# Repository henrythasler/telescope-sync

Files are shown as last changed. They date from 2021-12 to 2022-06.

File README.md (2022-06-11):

# Upgrading a Dobsonian-Telescope with Push-To Capabilities

This is about retrofitting a [Dobsonian Telescope](https://en.wikipedia.org/wiki/Dobsonian_telescope) with fancy electronics and means to indicate where the telescope is pointing at, to allow the observer to quickly find an object in the night sky. My motivation was born on a very cold evening shortly after I bought the telescope and I desparately tried to find Uranus in the night sky - and failed.

The resulting setup can, for example, be used with the excellent [Stellarium Plus](https://www.stellarium-labs.com/stellarium-mobile-plus/) App. 

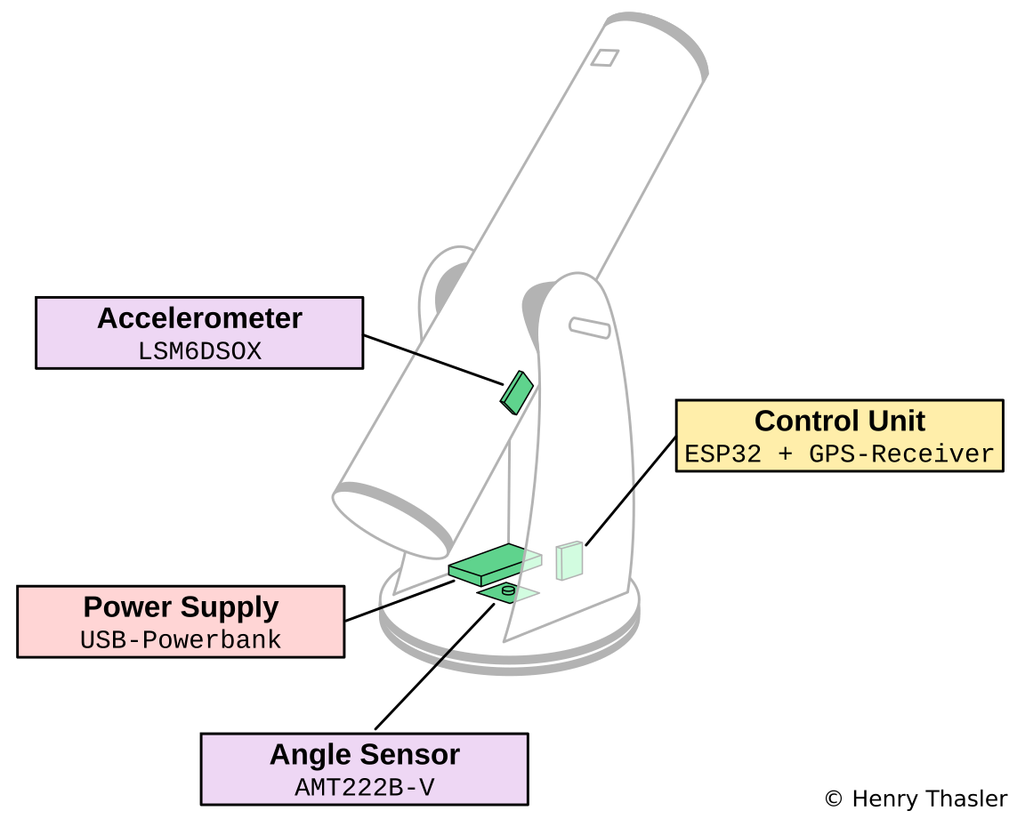
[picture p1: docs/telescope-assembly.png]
Telescope Assembly


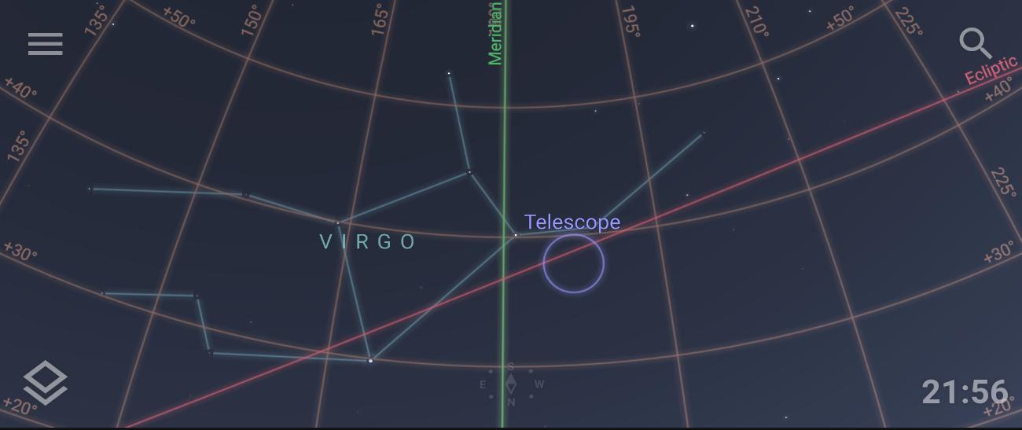
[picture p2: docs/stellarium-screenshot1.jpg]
Stellarium Screenshot


## Quick-Start-Guide

1. Connect power supply.
2. Connect Stellarium Plus via Bluetooth.
3. Wait for GPS location fix.
4. Point the telescope to a known target and set alignment point via Stellarium App.
5. Repeat step 4 to increase alignment precision.

## Introduction

A [Dobsonian Telescope](https://en.wikipedia.org/wiki/Dobsonian_telescope) is a type of telescope that uses an alt-azimuth mounting, which means you can rotate and tilt it. I'm using a [Sky-Watcher 8" Traditional](http://skywatcher.com/product/dob-8-traditional/) but the general method described here can be applied to any Dobsonian.

The term Push-to is generally referred to as a method to indicate (e.g. on a Smartphone-App) where the telescope is pointing at and thus allows to quickly find an object. 

The main design goals are:

1. Precision - I want this setup to be as precise a I can make it with hardware that is available to a hobbyist. 
2. Integration - The solution should integrate with existing astronomy-apps or -software.
3. Simplicity - Setup and installation must match the mobility of a Dobsonian telescope.
4. Wireless - No wires are needed to connect the user interface. Use Wifi or Bluetooth.
5. Ease-of-Use - Anyone should be able to use it with minimal guidance.

## General Concept

To map the current orientation of the telescope to a map of the night sky, we need the following information:

- Date and time
- Location
- Orientation of the telescope

With this information we can transform the orientation of the telescope from a horizontal (alt-azimuth) coordinate system to the equatorial coordinate system that astronomy apps use to indicate the actual position in the night sky where the telescope is pointing at. The critical information with the most influence on the resulting overall precision is the telescope's orientation.

## Overall Design and Result

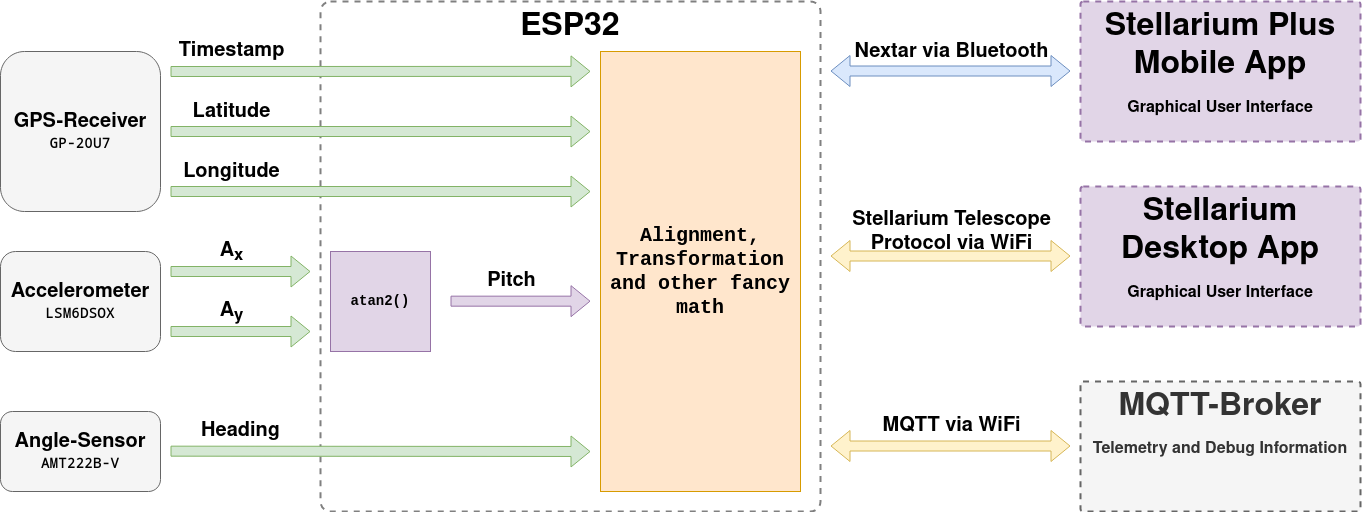
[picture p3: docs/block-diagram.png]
Block Diagram


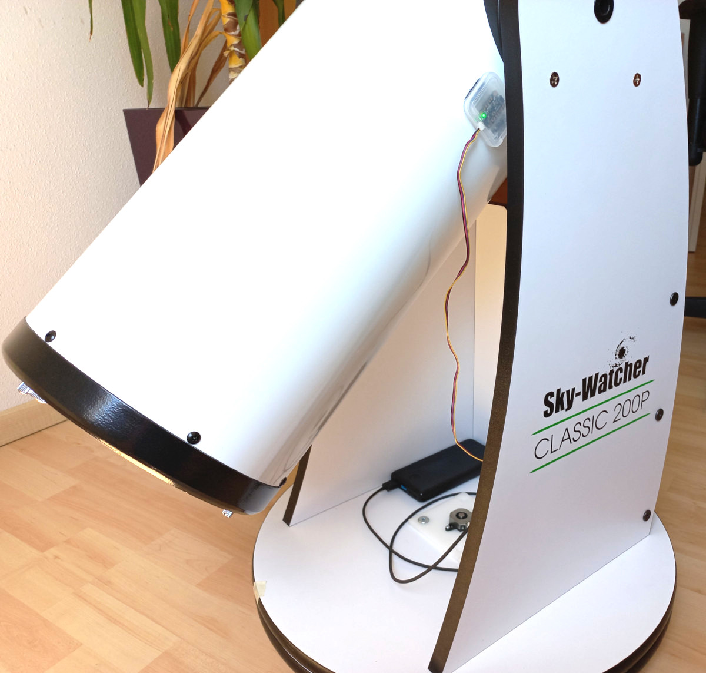
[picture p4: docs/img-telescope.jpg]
Telescope Picture
 

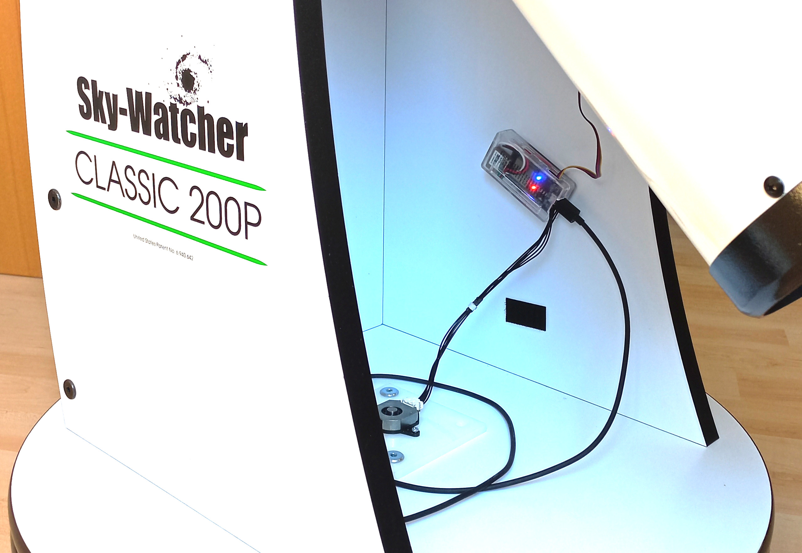
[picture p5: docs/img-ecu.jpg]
ECU Picture


### Stationary precision, noise

Pitch is filtered with 50-samples moving-average:

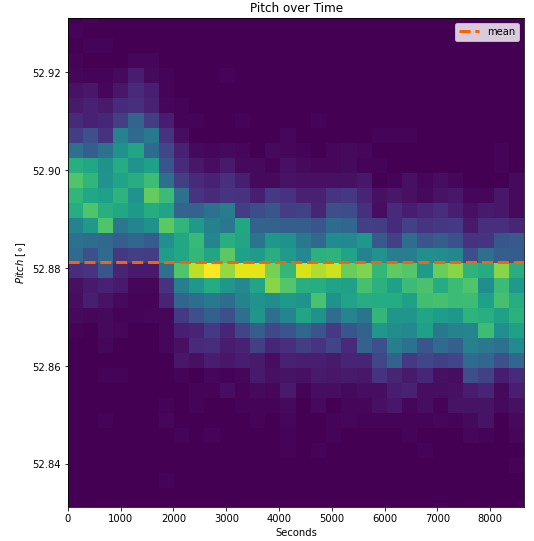
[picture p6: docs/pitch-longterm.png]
Chart Pitch Longterm


Heading is filtered with a simple IIR-Filter (decay=0.7):

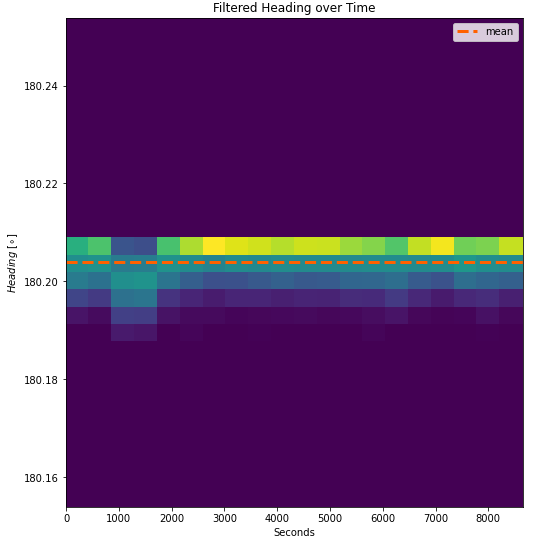
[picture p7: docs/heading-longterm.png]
Chart Heading Longterm


I'm really happy with the stationary precision and overall noise level.

Details about these test-results can be found in the [jupyter-lab notebook](docs/heading-pitch-longterm.ipynb) 

## Parts List

Part | Description | Datasheet | Price | Source
---|---|---|---|--
ESP32 DEVKIT V1 30-pin | Microcontroller | [ESP-WROOM-32 (30P)](https://github.com/TronixLab/DOIT_ESP32_DevKit-v1_30P) | <10€ | eBay
GP-20U7 | GPS-Receiver | [GP-20U7_Datasheet_v1 2.pdf](docs/GP-20U7_Datasheet_v1_2.pdf) | ~22€ | [Sparkfun](https://www.sparkfun.com/products/13740), [Berrybase](https://www.berrybase.de/en/audio-video/navigation/gps-empf-228-nger-gp-20u7-56-kan-228-le)
LSM6DSOX 6 DoF | Motion Sensor | [LSM6DSOX Datasheet](docs/lsm6dsox.pdf) | 12€ | [Berrybase](https://www.berrybase.de/en/sensors-modules/motion-distance/adafruit-lsm6dsox-6-dof-beschleugnigunssensor-und-gyroskop)
SD-Card Case | Housing for Motion Sensor | n/a | n/a | you will have one of these lying around
AMT222B-V | Angle Sensor | [AMT22-V Kit ](https://www.cuidevices.com/product/motion/rotary-encoders/absolute/modular/amt22-v-kit) | 50€ | [Mouser](https://eu.mouser.com/ProductDetail/CUI-Devices/AMT222B-V?qs=l7cgNqFNU1jQeqcgztT9Sw%3D%3D)
Molex 502578-0600 | Crimp-Housing for AMT22 | [CLIK-Mate Plug Housing](https://www.molex.com/molex/products/part-detail/crimp_housings/5025780600) | <1€ | [Mouser](https://eu.mouser.com/ProductDetail/Molex/502578-0600?qs=3OKVfsn1b5Ax%252B4TT0aiBNw%3D%3D)
Molex 79758-1011 | Cable Assembly for Crimp-Housing | [Pre-Crimped Lead CLIK-Mate](https://www.molex.com/molex/products/part-detail/cable_assemblies/0797581011) | 1€ | [Farnell](https://de.farnell.com/en-DE/molex/79758-1011/cable-assy-crimp-skt-skt-black/dp/3107351?CMP=i-ddd7-00001003)
Housing Raspberry Pi Zero | Housing for µC and GPS-Receiver | n/a | 4€ | [Berrybase](https://www.berrybase.de/en/raspberry-pi/raspberry-pi-computer/housing/for-raspberry-pi-zero/geh-228-use-gpio-referenz-f-252-r-raspberry-pi-zero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)
SparkFun Qwiic 500mm | Connector Cable | [Flexible Qwiic Cable - 500mm](https://www.sparkfun.com/products/17257) | 2€ | [Sparkfun](https://www.sparkfun.com/products/17257), [Berrybase](https://www.berrybase.de/en/sensors-modules/adafruit-stemma-qt-sparkfun-qwiic/cables/sparkfun-qwiic-flexibles-kabel-500mm)
Micro-USB Cable | Power Supply | n/a | <5€ | Amazon
USB-Power Bank | Power Supply | n/a | 15€+ | Amazon
Hook/Loop Fastener with Adhesive | Attach housings to telescope base | n/a | 5€ | Hardware store
Teflon Sealant Tape | Reduce tolerances | n/a | <5€ | Hardware Store
POM Plastic Sheet 6mm | Attach Angle Sensor | n/a | 10€ | Hardware Store
Steel Rod 25mm diameter | Attach Angle Sensor | n/a | 20€ | Hardware Store
various Fasteners | Parts assembly | n/a | <10€ | Hardware Store

## Hardware Setup

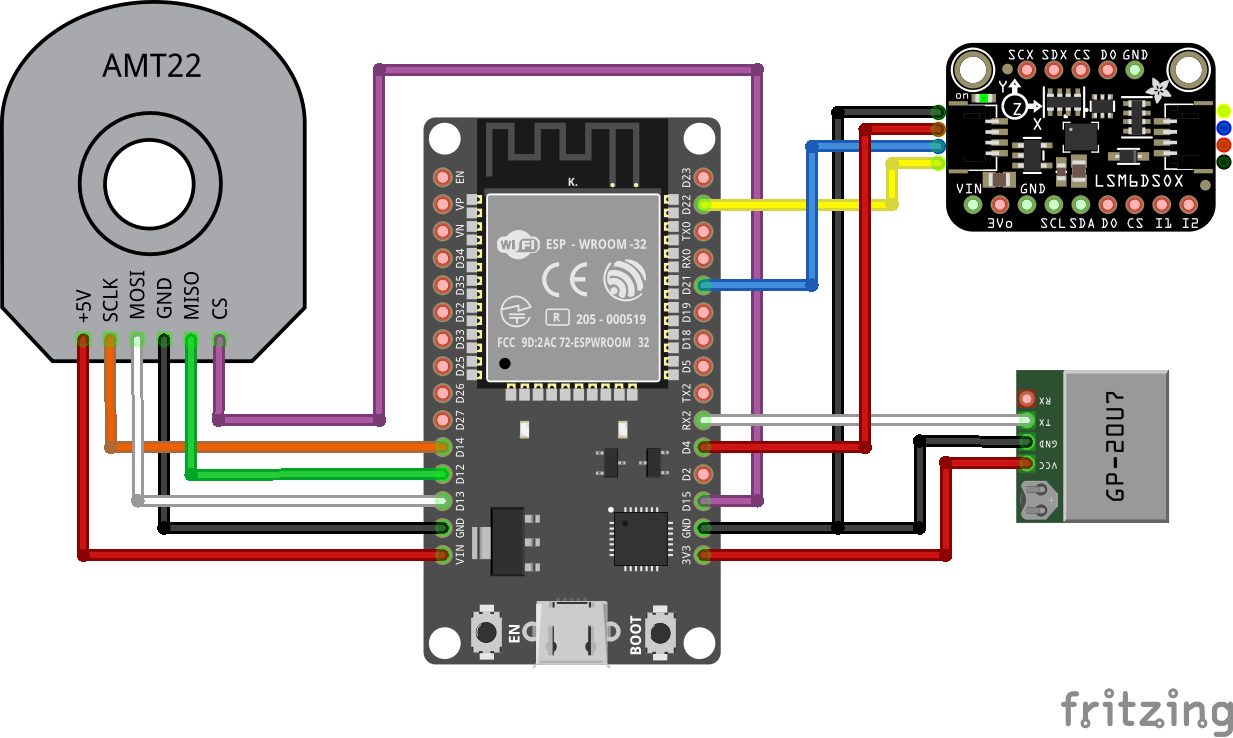
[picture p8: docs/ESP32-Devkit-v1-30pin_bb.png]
Wire Diagram


## Mechanical Construction

A FeeCAD-File is available in the `cad`-folder. The following parts need to be manufactured:

Part | Description | Drawing
---|---|---
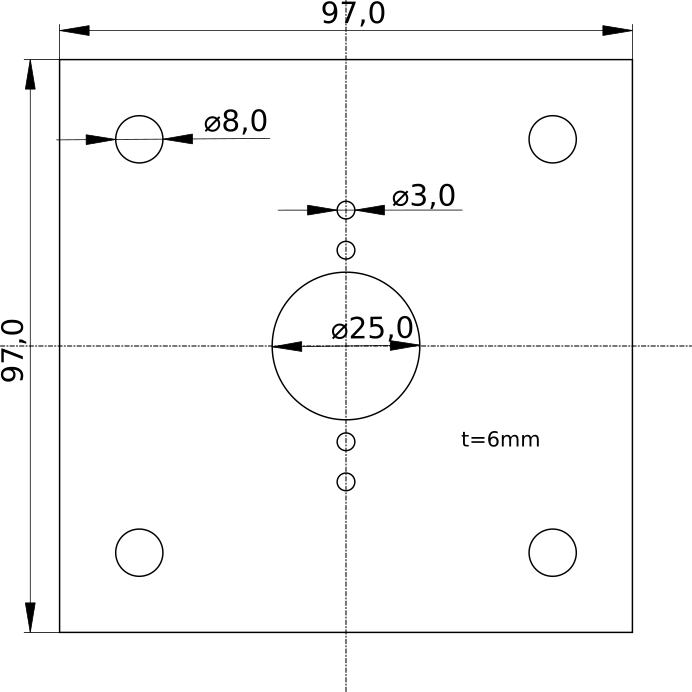
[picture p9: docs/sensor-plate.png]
Sensor Plate Drawing
Sensor Plate | The plate is attached to the center of the upper base plate of the dobsonian. The 25mm hole holds the flange of the bolt. The angle sensor is then centered over the bolt and attached to the sensor plate. | 
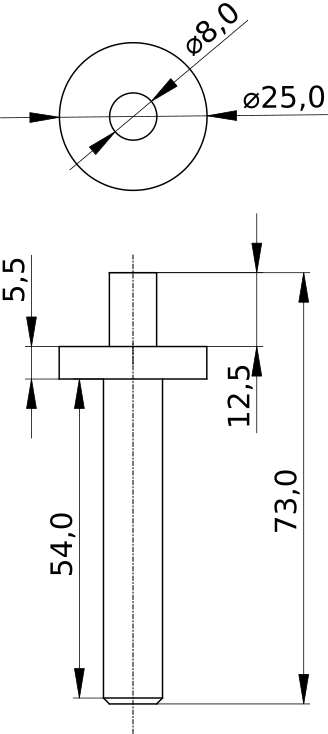
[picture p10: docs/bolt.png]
Bolt Drawing
Bolt | Holds the upper and lower plate together. Holding fixture for the angle sensor rotor. The long part needs an M10 thread for a self-locking nut.| 
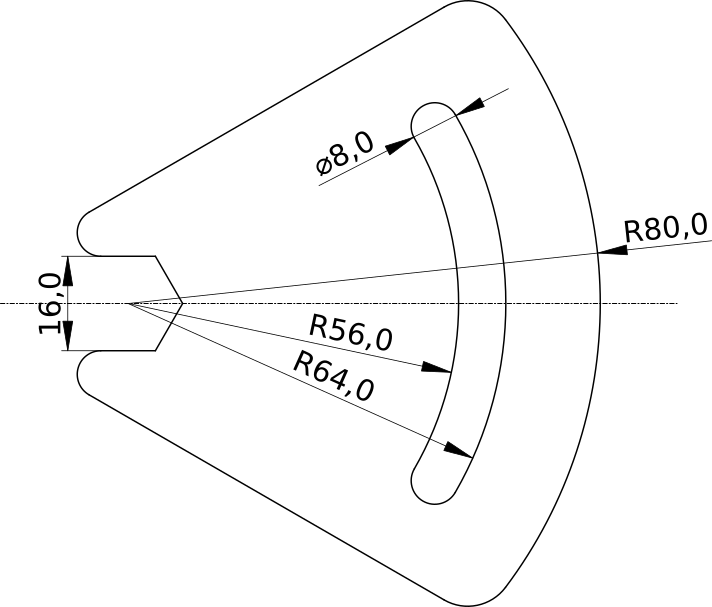
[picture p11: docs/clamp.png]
Clamp Drawing
Clamp | Attaches the bolt to the lower base plate. The hex-cutout goes over the self-locking-nut. | 

## Software

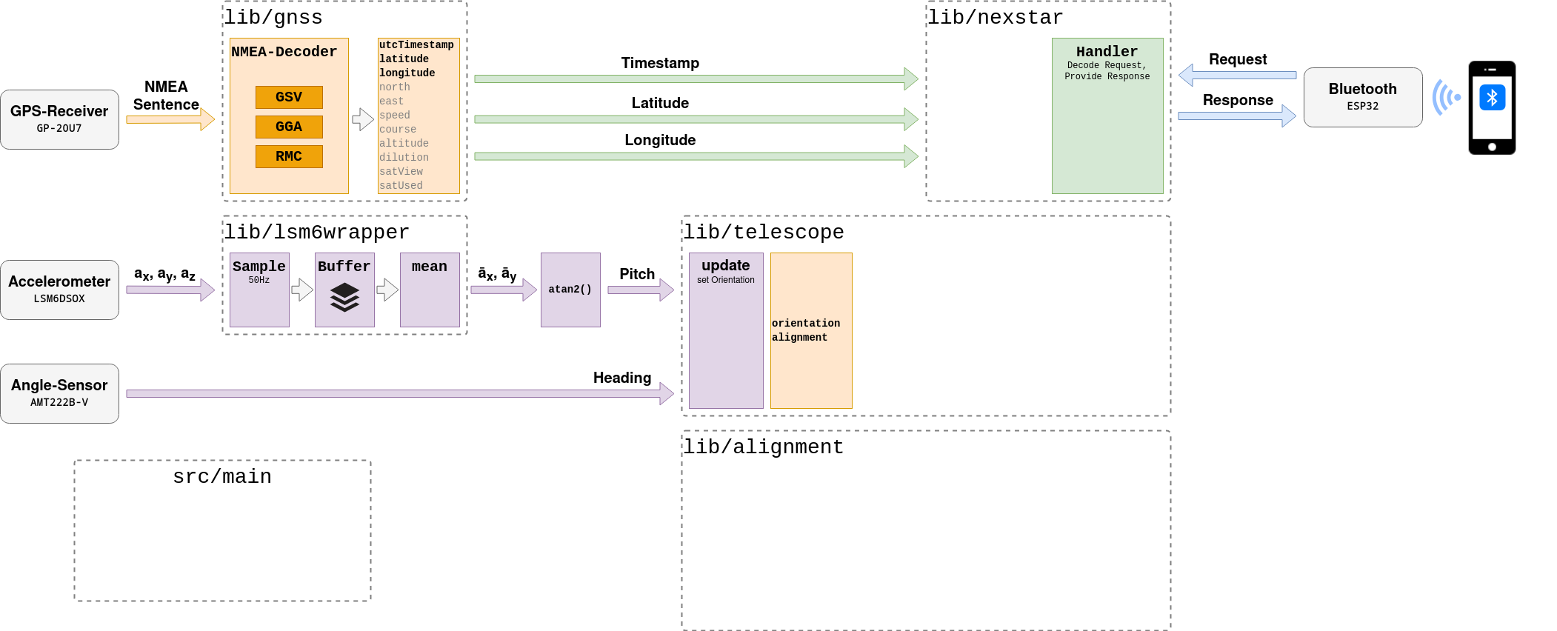
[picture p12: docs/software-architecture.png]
Software Architecture


## Telescope Alignment

As the telescope's orientation after installation, especially with the more mobile dobsonians, is likely to deviate from the ideal horizontal/vertical orientation and to compensate for sensor-offset in general, an alignment-step is needed before use.

The aligment method is based on the alignment models described by [THE EQMOD PROJECT - DOCUMENTATION & FAQs ](http://eq-mod.sourceforge.net/tutindex.html). To allow for maximum flexibility and precision, I implemented the following methods and algorithms:

- 1-point alignment for a real quick setup
- 2-point alignment to compensate for rotation errors
- n-point aligment with triangulated areas and automatic nearest triangle selection

The software picks the best method automatically, depending on the number of available alignment points.

For each alignment method, one (or multiple) transformation matrices are calculated using [2D affine transformations](https://medium.com/hipster-color-science/computing-2d-affine-transformations-using-only-matrix-multiplication-2ccb31b52181).

### Alignment Guide

Alignment is done by pointing the telescope to a know target (e.g. star) and sending the real position of that target to the control unit. This is usually done with the telescope control feature of [Stellarium Plus](https://www.stellarium-labs.com/stellarium-mobile-plus/).

### 1-Point-Alignment

Consider a simple example where the telescope is pointed at a target (like, a star) and the sensor output indicates that the position of that target is $\mathbf{S}_1$. We know that, based on our current location and time, the target should be at the reference position $\mathbf{R}_1$.

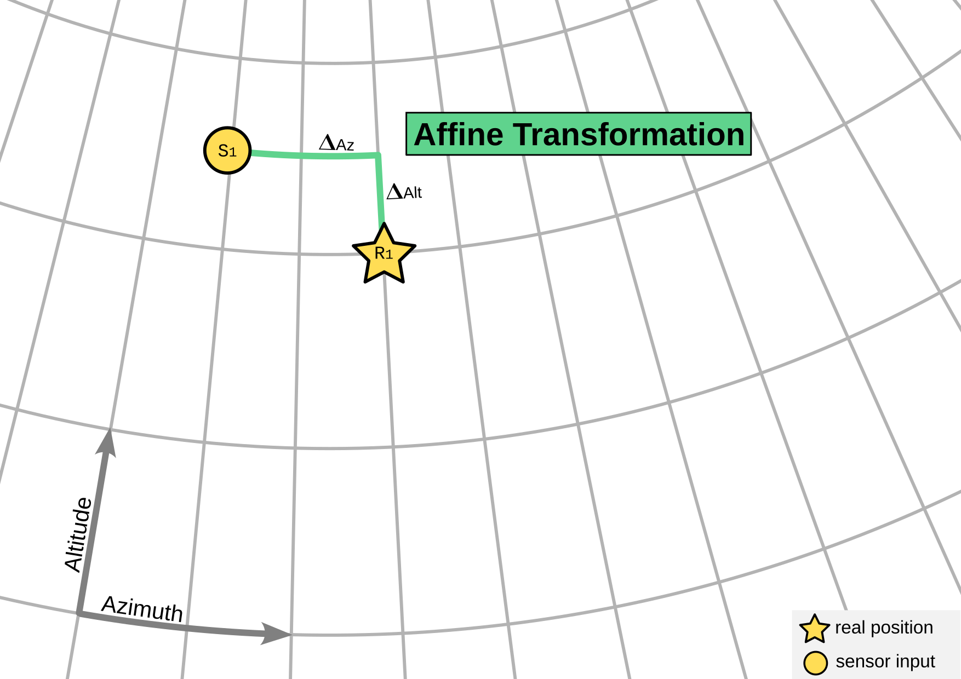
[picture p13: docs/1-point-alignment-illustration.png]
1-Point-Alignment


We can then calculate the difference $\Delta_{Az}$ and $\Delta_{Alt}$ and use these values to transform any given sensor input to it's real position:

$$\begin{pmatrix}
         R_{Az}\\
         R_{Alt} 
     \end{pmatrix} =
\begin{pmatrix}
         S_{Az} + \Delta_{Az} \\
         S_{Alt} + \Delta_{Alt}
     \end{pmatrix}
$$

This simple method clearly has it's limitations as it can't compensate for rotation and scale errors. To overcome this limitation, additional alignment points need to be added.

### 3-Point-Alignment

With 3 alignment points, we can draw lines between the sensor positions $\mathbf{S}_n$ resulting in a triangle. We can do the same with the real positions $\mathbf{R}_n$ and get another triangle. 

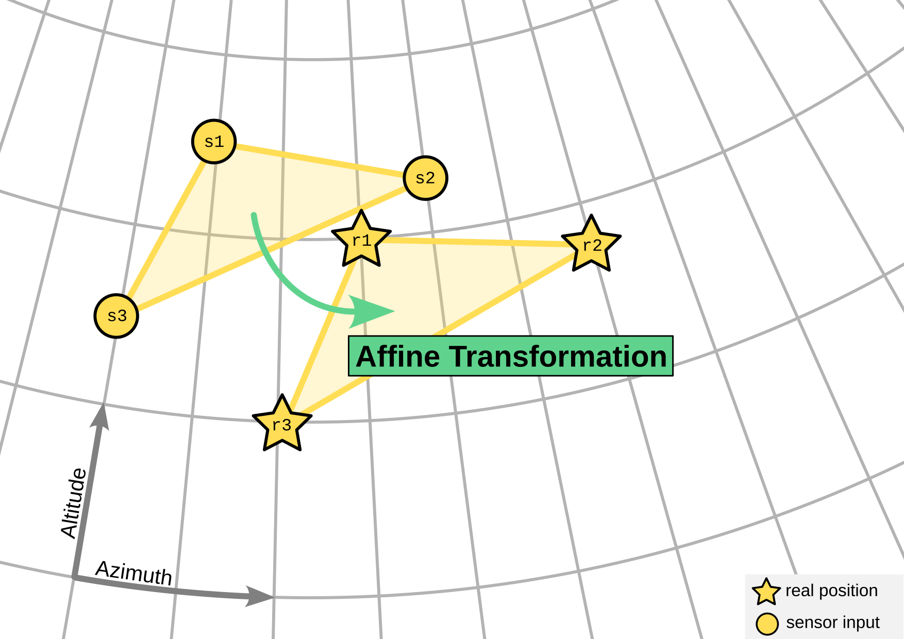
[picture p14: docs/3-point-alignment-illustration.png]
3-Point-Alignment


We can then calculate the affine transformation matrix $\mathbf{M}$ between the two triangles as follows:

$$\begin{aligned}
\mathbf{M} &= \mathbf{R} \times \mathbf{S}^{-1} \\
&= \begin{bmatrix}
         R_{1_{Az}} & R_{2_{Az}} & R_{3_{Az}}\\
         R_{1_{Alt}} & R_{2_{Alt}} & R_{3_{Alt}}\\
         1 & 1 & 1
     \end{bmatrix} \times
    \begin{bmatrix}
         S_{1_{Az}} & S_{2_{Az}} & S_{3_{Az}}\\
         S_{1_{Alt}} & S_{2_{Alt}} & S_{3_{Alt}}\\
         1 & 1 & 1
     \end{bmatrix}^{-1}
\end{aligned}$$

> Please note that in order to do the actual matrix calculations, we have to add a 3rd dimension ($z=1$) to each point.

We can then apply this transformation to any measured point $\mathbf{P}_S$ within the sensor input triangle to obtain the actual position $\mathbf{A}$ :

$$\begin{aligned}
\mathbf{A} &= \mathbf{M} \times \mathbf{P}\_S\\
\begin{pmatrix}
         A_{Az}\\
         A_{Alt}\\ 
         A_z 
     \end{pmatrix} &=      
    \begin{bmatrix}
         M_{11} & M_{12} & M_{13}\\
         M_{21} & M_{22} & M_{23}\\ 
         M_{31} & M_{32} & M_{33} 
     \end{bmatrix} 
     \times 
    \begin{pmatrix}
         P_{Az}\\
         P_{Alt}\\ 
         1 
     \end{pmatrix}
\end{aligned}$$

> $A_z$ can be ignored. We only need $A_{Az}$ and $A_{Alt}$.

This method can also be applied to points outside the alignment triangle but the precision will likely decrease with the distance to the triangle.

Solution? More alignment points!

### n-Point-Alignment

Adding more alignment points will give a better coverage of the sky but leads to another set of problems: 

1. New alignment points lead to new triangles.
2. Triangles might overlap.
3. Each triangle-pair (Sensor and Reference) can have it's own specific transformation matrix.

The solution to this is triangulation. We add all alignment points to an array and compute the resulting set of triangles using a [triangulation algorithm](http://paulbourke.net/papers/triangulate/). Whenever a sensor input needs to be transformed to the real position, we execute the following steps:

1. select the nearest triangle $T$ in our set of reference triangles.
2. use the triangle's specific transformation matrix $\mathbf{M}_T$, to calculate the real position

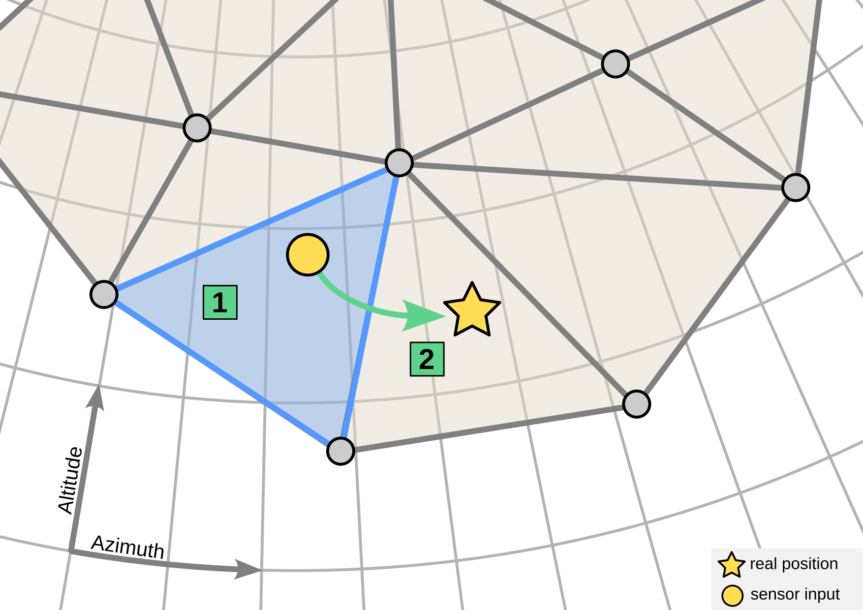
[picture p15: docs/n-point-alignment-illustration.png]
n-Point-Alignment


The actual horizontal position $\mathbf{A}$ is then derived from the sensor input $\mathbf{P}_S$ and the transformation matrix $\mathbf{M}_T$ as follows:

$$\mathbf{A} = \mathbf{M}_T \times \mathbf{P}_S$$

## User Interface

## Known Issues and Limitations

- Alignment near the zenith does not work very well due to the properties of the horizontal (Az-Alt) coordinate system.

## References

I used a lot of resources on the internet during this project. Here's a list of the most important:

### Similar Projects

- [vlaate/DobsonianDSC](https://github.com/vlaate/DobsonianDSC)
- [Control Your Telescope Using Stellarium & Arduino](https://www.instructables.com/Control-Your-Telescope-Using-Stellarium-Arduino/)
- [Arduino Star-Finder for Telescopes](https://www.instructables.com/Arduino-Star-Finder-for-Telescopes/)
- [SpotNik - StepTo / PushTo / Digital Setting Circles for EQ Mounted Telescopes Based on Arduino](https://www.instructables.com/SpotNik-StepTo-PushTo-Digital-Setting-Circles-for-/)
- [Instrumented Telescope with Raspberry Pi and orientation sensor](https://astrobeano.blogspot.com/2014/01/instrumented-telescope-with-raspberry.html)
- [Telescope pointing based on inertial measurement unit](http://www.doiserbia.nb.rs/Article.aspx?ID=1450-698X1794101V)
- [Accurate Telescope Mount Positioning with MEMS Accelerometers](https://arxiv.org/abs/1407.0035)

### Math

- [Calculating mean and apparent sidereal time](http://www2.arnes.si/~gljsentvid10/sidereal.htm)
- [Data: Converting Alt-Az to RA-Dec – Example](http://jonvoisey.net/blog/2018/07/data-converting-alt-az-to-ra-dec-example/)
- [International Astronomical Union Standards of Fundamental Astronomy](http://www.iausofa.org/)
- [The Astropy Project](https://www.astropy.org/)
- [Astronomical Calculations: Sidereal Time](https://squarewidget.com/astronomical-calculations-sidereal-time/)
- [Sidereal Time Calculator For Any Date, Time and Longitude](http://www.neoprogrammics.com/sidereal_time_calculator/index.php)
- [Local Sidereal Time](https://www.localsiderealtime.com/)
- [Sidereal time calculator](https://astro.subhashbose.com/siderealtime)
- [Converting RA and DEC to ALT and AZ](http://www.stargazing.net/kepler/altaz.html)
- [3D Rotation Converter](https://www.andre-gaschler.com/rotationconverter/)
- [THE EQMOD PROJECT - DOCUMENTATION & FAQs ](http://eq-mod.sourceforge.net/tutindex.html)
- [How to find a transformation matrix, given coordinates of two triangles in R2](https://math.stackexchange.com/questions/557507/how-to-find-a-transformation-matrix-given-coordinates-of-two-triangles-in-r2)
- [Computing 2D affine transformations using only matrix multiplication](https://medium.com/hipster-color-science/computing-2d-affine-transformations-using-only-matrix-multiplication-2ccb31b52181)
- [Learn How to Write Markdown & LaTeX in The Jupyter Notebook](https://towardsdatascience.com/write-markdown-latex-in-the-jupyter-notebook-10985edb91fd)
- [tomstewart89/BasicLinearAlgebra](https://github.com/tomstewart89/BasicLinearAlgebra)
- [Efficient Triangulation Algorithm Suitable for Terrain Modelling, Paul Bourke, 1989](http://paulbourke.net/papers/triangulate/)
- [Use Markdown to display mathematical expressions on GitHub](https://docs.github.com/en/get-started/writing-on-github/working-with-advanced-formatting/writing-mathematical-expressions)
- [FIIIR! - Design FIR & IIR Filters](https://fiiir.com/)

### Orientation Sensor

- [Bosch Sensortec MEMS BNO055 sensor driver](https://github.com/BoschSensortec/BNO055_driver)
- [AltIMU-AHRS](https://github.com/jremington/AltIMU-AHRS)
- [Using an Accelerometer for Inclination Sensing](https://www.analog.com/en/app-notes/an-1057.html)

### GPS, GNSS, NMEA

- [GPS - NMEA sentence information](http://aprs.gids.nl/nmea/)
- [Common NMEA Sentences](http://www.satsleuth.com/GPS_NMEA_sentences.aspx)

### Hardware

- [Comparing Gyroscope Datasheets](https://learn.adafruit.com/comparing-gyroscope-datasheets)
- [DOIT ESP32 DevKit-v1 (30P)](https://github.com/TronixLab/DOIT_ESP32_DevKit-v1_30P)

### ESP32 Programming

- [How to format strings without the String class](https://cpp4arduino.com/2020/02/07/how-to-format-strings-without-the-string-class.html)
- [C++ Core Guidelines](http://isocpp.github.io/CppCoreGuidelines/CppCoreGuidelines)
- [ESP32: Getting started with Bluetooth](https://www.electrosoftcloud.com/en/esp32-getting-started-with-bluetooth/)
- [ESP32 Arduino Tutorial: 38. Serial over Bluetooth - Client connection event](https://www.dfrobot.com/blog-1203.html)

### Stellarium

- [RemoteControl plugin HTTP API description ](http://stellarium.org/doc/head/remoteControlApi.html)
- [Telescope Control plug-in](http://stellarium.sourceforge.net/wiki/index.php/Telescope_Control_plug-in)
- [NexStar Communication Protocol v 1.2](https://www.celestron.com/pages/manuals)

### Astronomy related

- [Light pollution map](https://www.lightpollutionmap.info/)
- [NexStar Resource Site](https://www.nexstarsite.com/index.html)

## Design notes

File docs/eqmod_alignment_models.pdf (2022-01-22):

# EQASCOM Alignment

Page 1 of 28

## Introduction

This document will attempt to explain how EQASCOM implements its alignment routines to achieve the highest possible GOTO Accuracy. We shall present the different alignment configurations possible and explain what type of mount/OTA errors can be corrected.

## Points v Stars

Its quite likely that whilst reading EQMOD documentation and/or forum postings you will come across references to “Alignment Stars” and N-Star alignment. Certainly until recently this was the terminology we used, however, with version EQASCOM V1.17 we have re-worked our user interfaces to use refer to Alignment Points, N-Point etc. Whilst it is certainly the case that most folks will use stars as handy reference points when performing alignment we found that new users were often confused about there relevance to the pointing model. The term Point is preferred because:

- Stars do not hold a fixed position with respect to the observer, they are constantly moving. The alignment model dos not move and holds true irrespective of the subsequent position of the stars used to create it.
- Alignment can be archived using plate solving which does not require centring the telescope on a specific target star.

## Pointing Correction Transformations

EQASCOM has two basic telescope pointing correction methods used in computing for the location of a target object based on a number of reference points.

Nearest Point Transformation

This uses a Delta mapping method (Delta-RA, Delta-DEC) where simple coordinate transformation is used based on the distance (in RA and in DEC units) between the known Catalog Coordinate of an alignment point and the actual location of the point. The actual location of the point is measured by a user using a reticle eyepiece.

3–Point Transformation

The second method uses the AFFINE/TAKI Coordinate transformation process based on three reference points and their respective measured locations using a reticle eyepiece.

Page 2 of 28

### Nearest Point Transformation Model

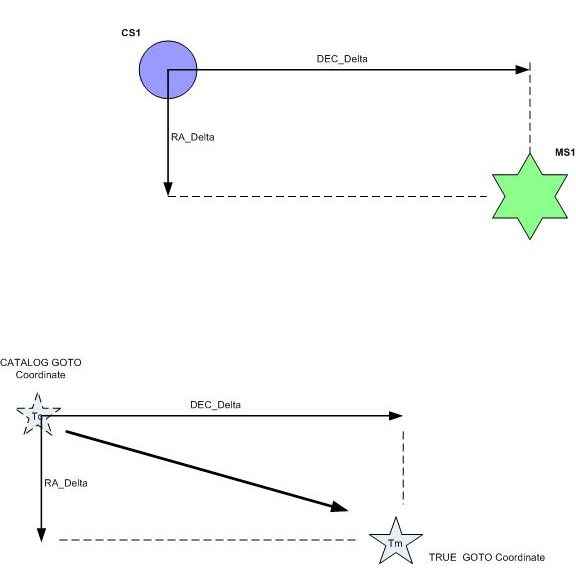
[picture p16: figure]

FIGURE 1: EQMOD Nearest Point Transformation method using the basic Delta-RA and Delta-DEC Distance mapping technique

In the 1 Point model, EQASCOM simply gets the location of the measured point and records the RA and DEC distance between the Planetarium Database RA and DEC coordinates (Catalog Coordinates) of the point/star (CS1) and the mount's reported RA and DEC coordinates of the measured point (MS1) as captured during the alignment procedure. The RA_delta and DEC_delta (distance) values are then used to compute for the location of any target object (Tm) based on the object's Planetarium Database Catalog coordinates (Tc).

Page 3 of 28

### The 3-Point Transformation Model

For the 3-Point transformation method, the AFFINE/TAKI coordinate transformation matrix operation is used to compute for the apparent location of an object (Tm) based on the RA/DEC coordinates three reference Catalog point (CS1,CS2, CS3) and the measured RA/DEC coordinate of these points (MS1,MS2,MS3) as captured during the alignment process. The target object's coordinates (Tm) is then computed by AFFINE coordinate transformation on the Catalog (CS1-3), Measured (MS1-3), and Catalog Coordinates of the target object (Tc).

The most accurate gotos are obtained INSIDE the triangle bounded by the three alignment points. For locations outside the triangle EQASCOM automatically switches to use the Nearest Point (1-Point) model.

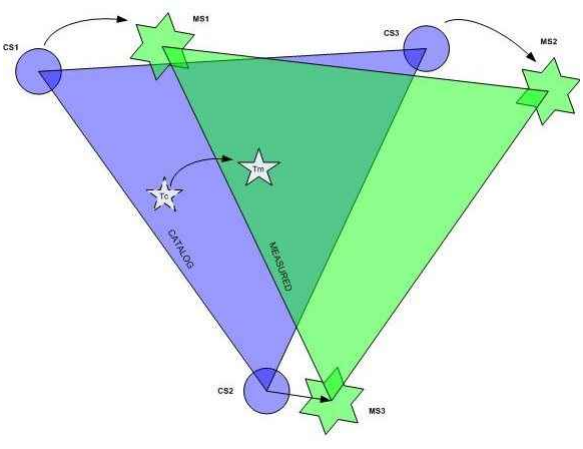
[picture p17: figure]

FIGURE 2: EQMOD 3-Point Transformation Method using the 3-point AFFINE Coordinate Transformation

Page 4 of 28

## Mount/OTA Error Modelling using Nearest Point and 3-Point Coordinate Transformation

EQASCOM's mount error modelling scheme uses a coordinate transformation process between the celestial sphere and the mount's stepper coordinate space. This basically is a point-to-point (mount-to-sky) mapping for any errors such as X-Y shifts, rotation, magnification, reduction, and one-sided skews which translate to polar alignment, cone errors, OTA axis alignment errors, RA and DEC axis errors, etc.

With Nearest Point error modelling, only the RA coordinate and DEC coordinate shifts (X-Y shifts) are accounted for. It does not account for rotations, magnification, reduction, and coordinate skews where most of the mount errors are present.

With 3-point error modelling, X-Y coordinate shifts, rotations, magnification, reduction, one-side skews are being accounted such that most of the alignment errors present on the mount and the OTA's optical axis are being compensated. The following figures illustrate all kinds of scope 3-point modelling errors that can be present on any setup.

### 3-Point X-Y Shifts Errors

Figure 3 and 4 shows a sample measured X and Y shift errors on all three stars with respect to the Catalog Points. If such errors are measured on one side of the meridian for example (Figure 5), the mount could have exhibited a misalignment from the true RA home position and DEC home position which is commonly present on manually aligned Mount to OTA Home positions (Counter weights shaft pointed down, OTA pointing north or south). This is basically normal as we typically start from a "manually home positioned" mount.

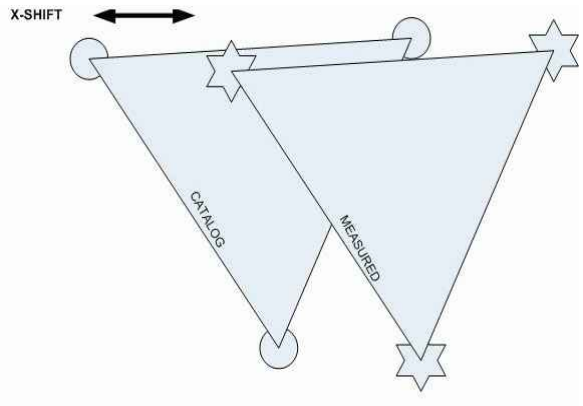
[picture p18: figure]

FIGURE 3: Three-Point X-Shift error representation

Page 5 of 28

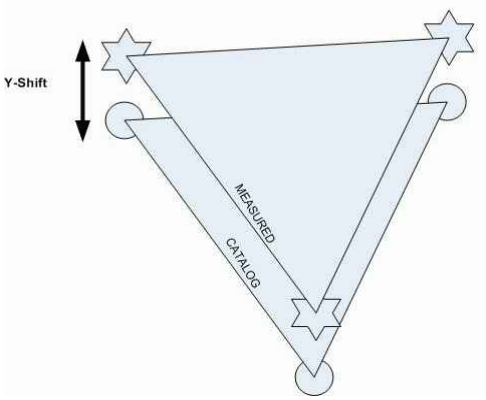
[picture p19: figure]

FIGURE 4: Three-Point Y-Shift error representation

Page 6 of 28

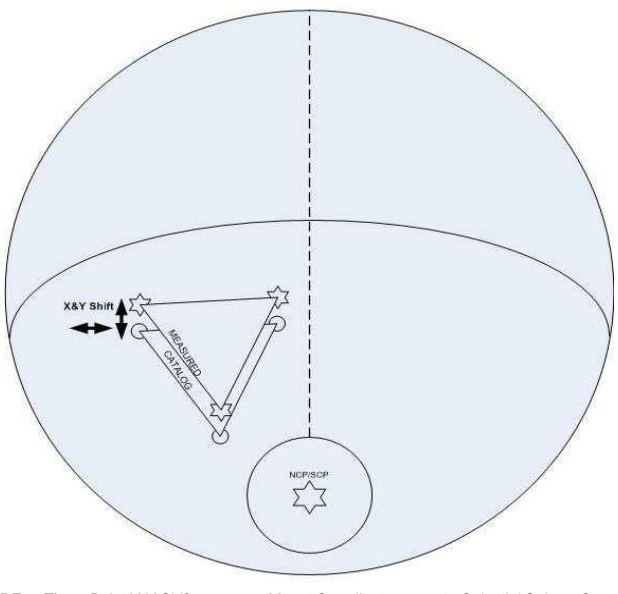
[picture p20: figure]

FIGURE 5: Three-Point X-Y Shift error on a Mount Coordinate space to Celestial Sphere Coordinate space

### Three-Point Rotation Errors

In Figure 6 the measured stars exhibit a rotation with respect to the Catalog coordinates. If such rotation is measured for example at the meridian side (figure 7), the mount has exhibited an error shift on the Azimuth to NCP/SCP. If a rotation is present for example on the horizon side (Figure 8), the mount has exhibited an error shift on the Altitude to NCP/SCP. The angle of rotation is actually the measured drift slope on EQASCOM's Polar alignment computations. The higher the angle of rotation, the higher the drift slope will be, which basically translates to Polar Alignment shift errors. Three-point rotation errors is a clear indication of the mount's RA axis not being parallel to the Earth's axis.

Page 7 of 28

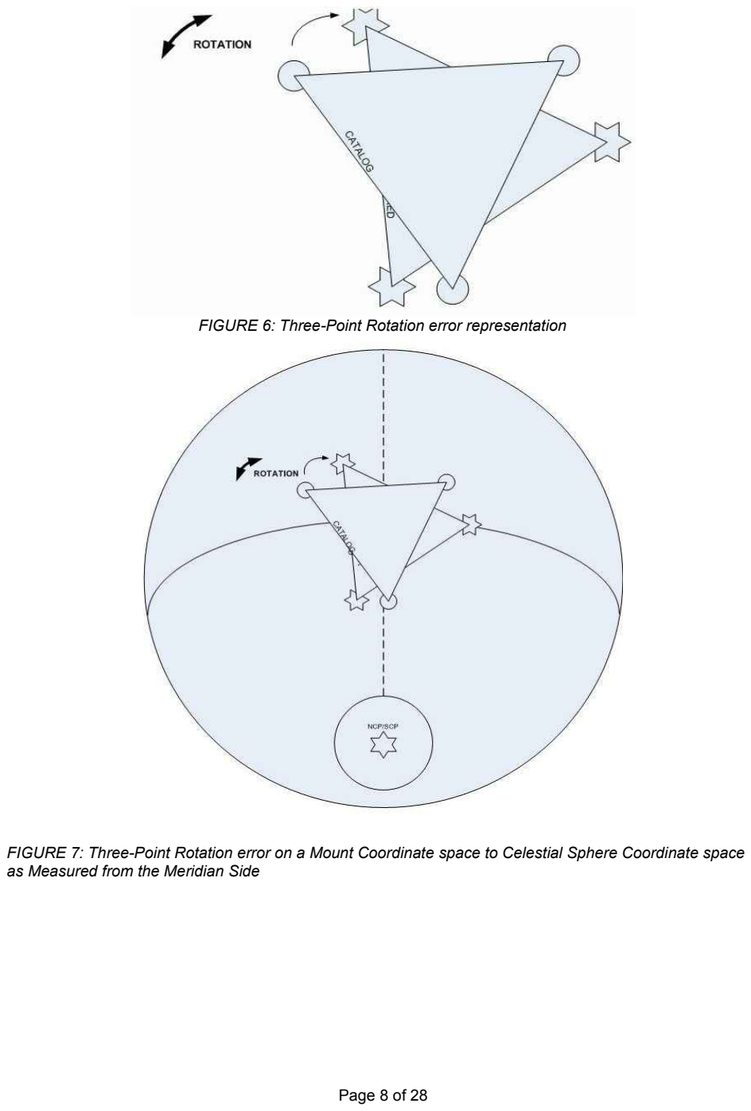
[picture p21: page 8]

FIGURE 6: Three-Point Rotation error representation

FIGURE 7: Three-Point Rotation error on a Mount Coordinate space to Celestial Sphere Coordinate space as Measured from the Meridian Side

Page 8 of 28

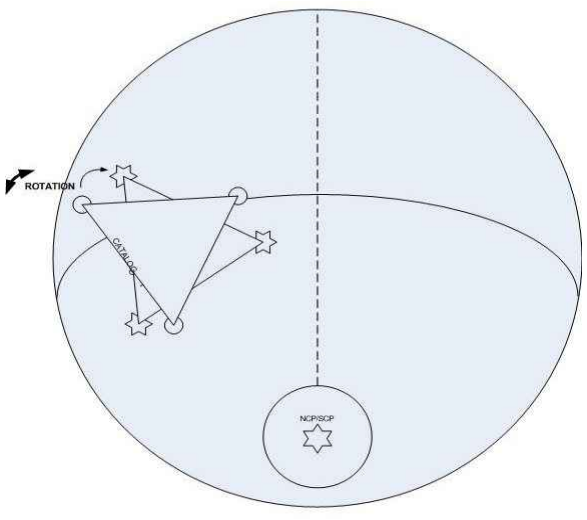
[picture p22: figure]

FIGURE 8: Three-Point Rotation error on a Mount Coordinate space to Celestial Sphere Coordinate space as Measured from the Horizon Side

Page 9 of 28

### Three-Point Magnification-Reduction Errors

In Figure 9, the area of the triangle formed by the measured points is greater or less than the area of the triangle formed by the 3 Catalog points. If such errors are measured for example at the meridian (Figure 10), then the mount could have exhibited the classic case of CONE errors. The shift is usually away from the meridian and towards or away from the horizon. This basically means that the OTA's optical axis is NOT perpendicular to the mount's DEC Axis.

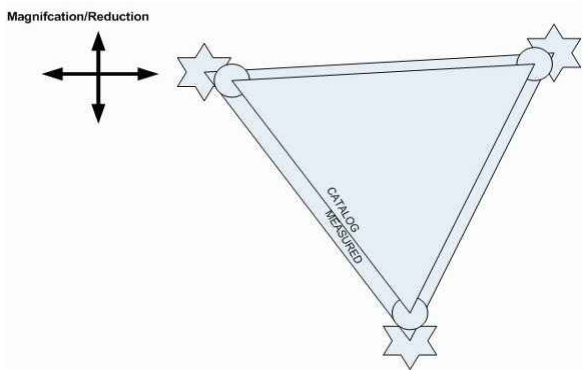
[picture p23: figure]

FIGURE 9: Three-Point Magnification-Reduction error representation

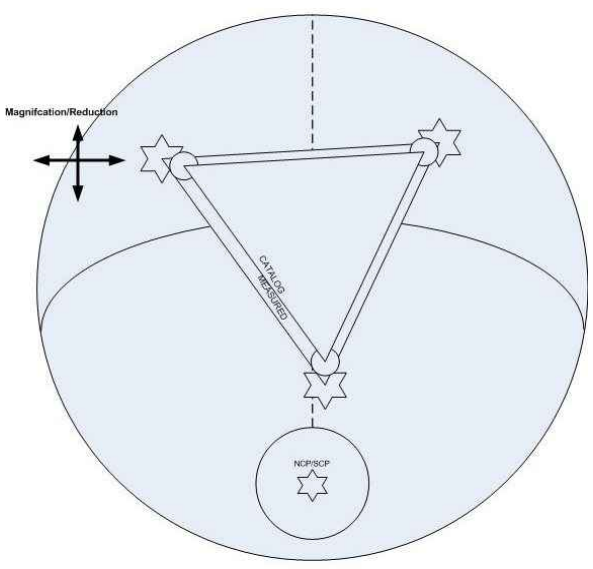
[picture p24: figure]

FIGURE 10: Three-Point Magnification-Reduction error on a Mount Coordinate space to Celestial Sphere Coordinate space

Page 10 of 28

### Three-Point 1 Side Skew Errors

Ideally, the AREA of the triangle formed by the three Catalog Points should be identical to the triangle formed by the three measured Points. If one of the points has exhibited a shift (Figure 11) and there are no rotation or magnification errors, then there is a skew and the AREA of both triangles will not be equal. Such skew when measured for example at any part of the sky (Figure 12), then there is the classic case of mount to OTA flexures. Mechanical flexures are typically isolated and OTA position angle specific and the influence on the three alignment stars are not constant thus creating a skew on the alignment stars.

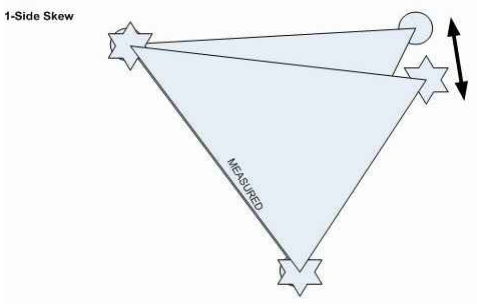
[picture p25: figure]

FIGURE 11: Three-Point 1 sided skew error representation

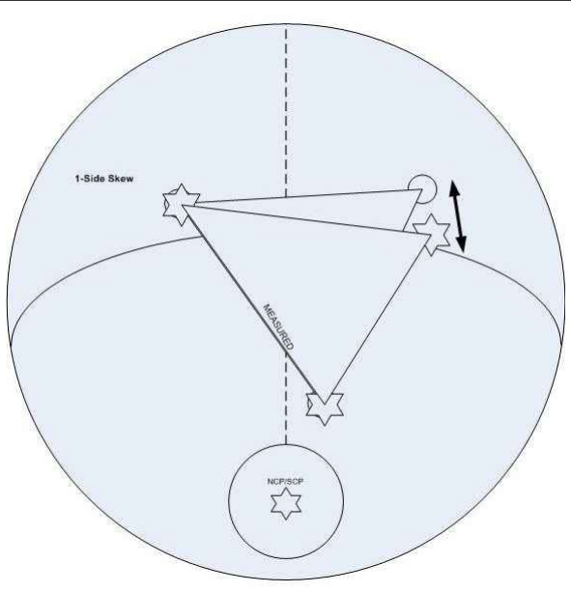
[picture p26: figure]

FIGURE 12: Three-Point One-Sided skew error on a Mount Coordinate space to Celestial Sphere Coordinate space

Page 11 of 28

### Three-Point Combination Errors

With a Three-Point combination (Figure 13 - X-Y Shift, Rotation, Magnification-Reduction, 1sided skews), the algorithm basically models most of the mount's misalignment errors. As the mount+OTA sees it on the sky (Figure 14), the algorithm practically compensates for these errors and should easily provide you the most accurate GOTO pointing model for your mount.

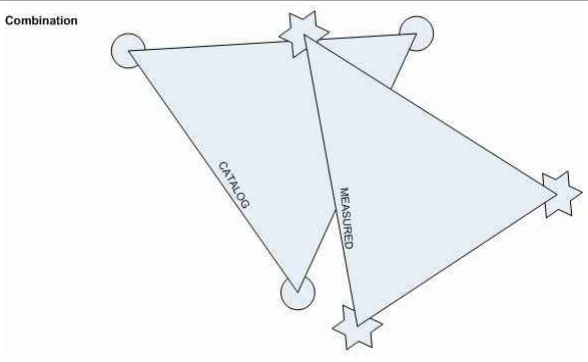
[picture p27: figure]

FIGURE 13: Three-Point Combnination X-Y Shift, Rotation, Magnification-Reduction, 1Sided Skew error representation

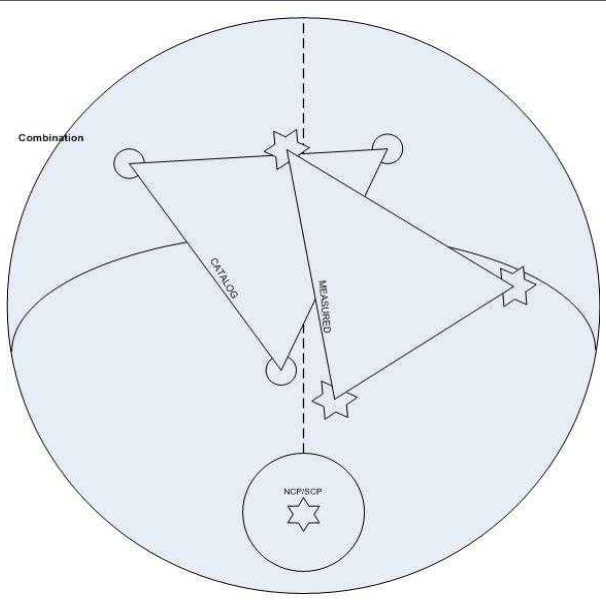
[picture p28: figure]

FIGURE 14: Three-Point Combnination X-Y Shift, Rotation, Magnification-Reduction, 1Sided Skew error on a Mount Coordinate space to Celestial Sphere Coordinate space

Page 12 of 28

## EQASCOM Pointing Models

So far we've looked at the pointing transformations that EQASCOM has at its disposal. How and when EQASCOM uses these transformations is the key to the Pointing Model.

EQASCOM provides a N-Point pointing model. Users can define pretty much as many alignment points as they wish (up to 1000 maximum). The user also has some control over which pointing transformation algorithms are used.

Nearest Point

Nearest Point simply searches through the current alignment list to find the alignment point nearest to target position. Once the nearest star is found a transformation is preformed based upon the data associated with that point.

3-Point

EQASCOM will automatically choose the best Transformation method.

- If less than 3 points have be defined it will use a Nearest Point transformation
- If 3 or more points are defined then EQASCOM iterates through all triangle combinations possible using the 50 nearest alignment points to establish which triangle has its centre closest to the target position. The three alignment points that make up that triangle are then used for pointing correction. The diagram below illustrates this process. There are four stars in the alignment list and as a result there are four possible alignment triangles.

Page 13 of 28

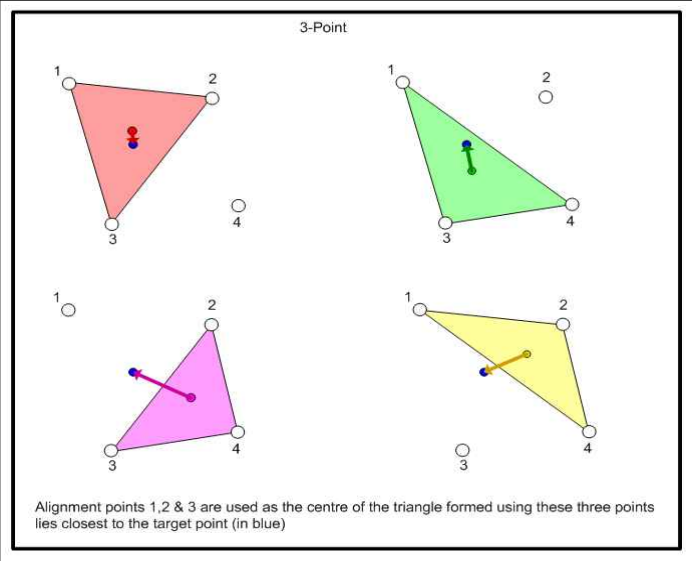
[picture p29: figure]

- Where a target falls outside of the bounds of a 3-Point triangle EQASCOM will automatically switch to using the Nearest Point transformation.

Page 14 of 28

- A potential problem occurs where where 3-Point triangles span the meridian, particularly if you have a reflecting telescope where mirror flop many be significant factor. EQASCOM has a “Pierside Points Only” checkbox which will ensure that only points on the same side of the meridian as the target point to be used in transformation calculations.
- When using a three point transform it is clearly important that all three alignment points used have been accurately calibrated. One badly calibrated point can have an impact over a large area of sky. The digram below compares the the area of influence the blue alignment point has for both Nearest Star (left) and Three Star (right) transformations.

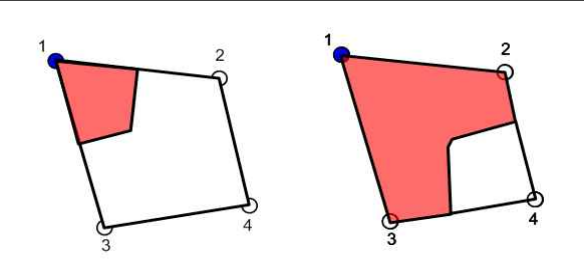
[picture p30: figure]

- As the number of alignment points increase the areas of influence of each individual point become increasingly more complicated to visualise. If you have any doubts about the accuracy of any alignment points within a MultiPoint model you may find better pointing is

Page 15 of 28 achieved by switching to using a Nearest Point algorithm which limits thee areas of influence of badly calibrated points.

Page 16 of 28

## Choosing which Alignment method to use

The following sections will give you some basic guidelines on choosing which alignment method to use. EQMOD provides all of these alignment methods at the disposal of the user so that the system can easily adapt for any mount+OTA alignment conditions,

### 1 Point Alignment

When fewer than three points are present EQASCOM will automatically apply a Nearest Point transform. A One Point alignment (Figure 15) only compensates for X-Y shift errors and should work with the following:

- User has opted for 1 star sync for quick alignment/imaging/observing session. This works best if the target object is situated near the alignment star
- 1 Point alignment would only be suitable for "all sky" pointing if :
- The mount is accurately polar aligned
- There are no CONE ERRORS and the OTA's optical axis is always perpendicular with the DEC axis
- Minimized Flexure errors
- No (or minimized) mechanical slop on both RA and DEC gears

It is best to choose the alignment point to be near the celestial equator and at least 30 to 45 degrees from the horizon to minimize any light refraction shifts which are prominent near the horizon.

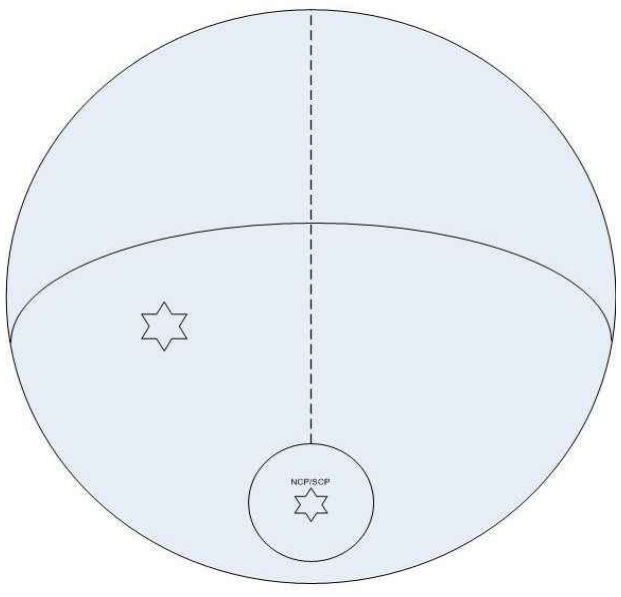
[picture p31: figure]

Figure 15: One Point Alignment as measured on one side of the Meridian

Page 17 of 28

### 2 Point Alignment

When fewer than three points are present EQASCOM will automatically apply a Nearest Point transform2-Point alignment is basically a dual 1-Point modelling scheme. This works best if one of the alignment points is situated on one side of the meridian with the second alignment point on the other side of the meridian (Figure 16).

- Mount should be accurately polar aligned as the 1-Point model does not account for Rotation Errors.
- There should be minimal or no MOUNT+OTA FLEXURES as the 1-Point model only accounts for flexures near the alignment stars. Actually a flexure error on where the alignment point is located could easily influence the entire meridian side amplifying the GOTO pointing error.
- CONE Errors are meridian side specific and can be compensated by a dual 1-point model although GOTO errors due to CONE issues
- tend to increase as you target objects near the north our south part of the sky.
- It would be best to choose points near the celestial equator to even out the errors induced by cone and flexure errors.

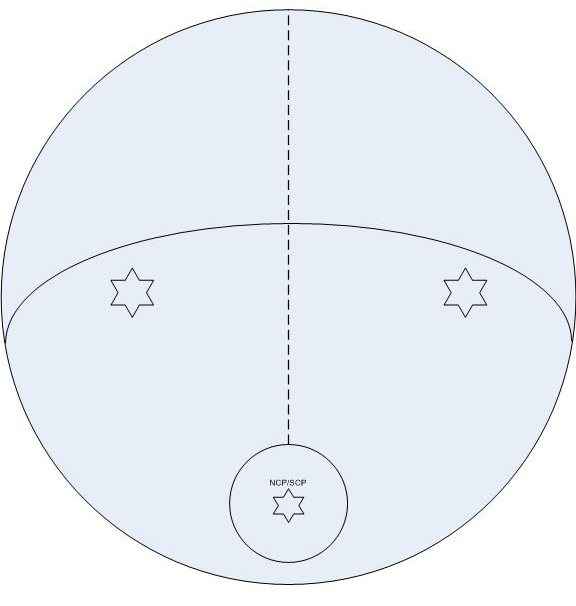
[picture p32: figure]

Figure 16: Two Point Alignment as measured on both sides of the Meridian

There must be a serious question as to whether folks should bother with two point alignment in practice particularly given that three point alignment provides much better correction.

Page 18 of 28

### 3 Point Alignment (3-Point+Nearest Transform)

Three Point alignment (Figure 17) is the basic implementation of the 3-point model pointing scheme. It accounts for all error (shifts, rotations, etc) however only up to a certain extent;

- The three points should be widely spaced as you are averaging out the errors induced on the four corners of the sky.
- Very sensitive to meridian flips as the flexure errors on one side of the meridian can easily influence the pointing accuracy of the other side of the meridian

To recover from this issue the user can switch to EQASCOM's "Nearest Point" mode and the driver will revert to a 1-point model pointing scheme disabling the affine triangle and re-using the three alignment points as a TRIPLE 1-point pointing model. EQMOD will simply choose the nearest point based on the target GOTO object and apply the usual X-Y shift modelling compensation.

- GOTOs are mostly accurate within the triangle formed by the three alignment point. GOTO accuracy tend to decrease as you put your target objects OUTSIDE the triangle
- Obviously, two of the three points are always situated on one side of the meridian and GOTOs are likely to be more accurate on this side.

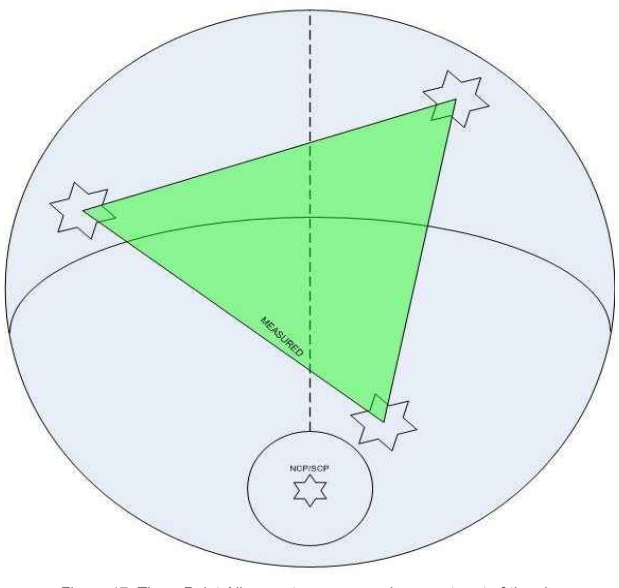
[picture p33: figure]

Figure 17: Three Point Alignment as measured on most part of the sky

Page 19 of 28

### 4 Point Alignment (3-Point+Nearest)

Four point alignment still uses the 3-Point model pointing scheme as driver dynamically chooses the three of the four nearest alignment points to process the AFFINE/TAKI transformation. The four star alignment accuracy is almost identical with the 3-star alignment except that with four stars (Figure 18), you balance the number of alignment stars on both sides of the meridian. This will make the pointing accuracy consistent on both sides of the meridian unlike with the 3-point, accuracy is higher on the side of the meridian where two of the three points are located.

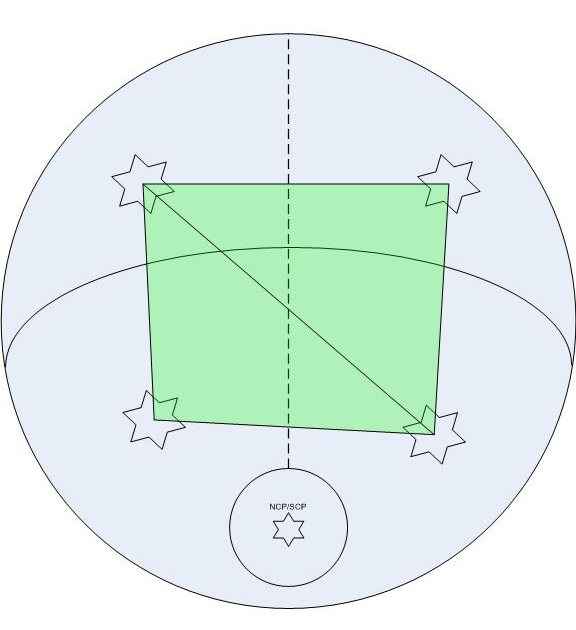
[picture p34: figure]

Figure 18: Four Star Alignment as measured on four corners of the sky

Page 20 of 28

### 6 Point Alignment (3-Point+Nearest Transform)

A Six point alignment layout (Figure 19) provides better pointing accuracy than the three or four points as it "ISOLATES" any "INTER-MERIDIAN" dependency errors. EQASCOM will still apply the 3-point model scheme but dynamically choose the three nearest alignment points from the six available to implement the AFFINE/TAKI transformation. Each side of the meridian will then have its own independent 3-point model scheme isolating any flexure influence on the other side of the meridian providing the user close to arcseconds of pointing accuracy specifically within the area covered by the triangles on each side of the meridian. This method is also best for measuring the Polar Alignment of your mount.

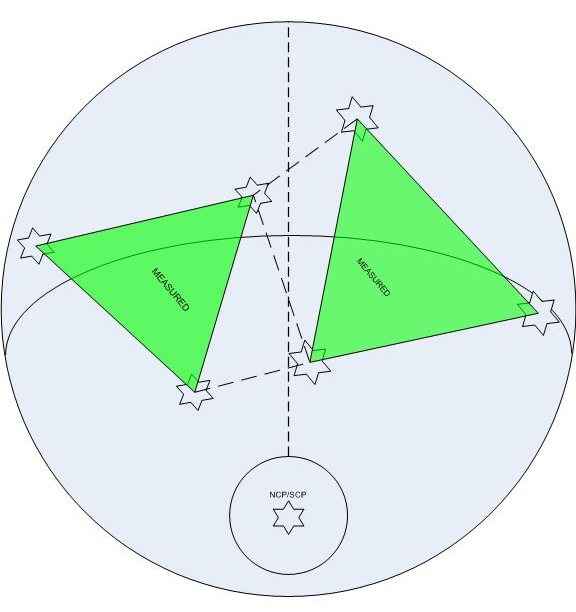
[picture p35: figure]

Figure 19: Six Point Alignment as implemented with 3 points on one side of the Meridian and another 3 on the other side

Page 21 of 28

### 12 Point Alignment (3-Point+Nearest Transform)

A twelve point alignment method provides MULTIPLE 3-point modelling on four corners of the sky (Figure 21) which minimizes BOTH the inter-meridian dependency errors AND North to South dependency errors. This addresses mostly FLEXURE error isolations on the four corners of the sky aside from the usual polar, shift, cone, etc.

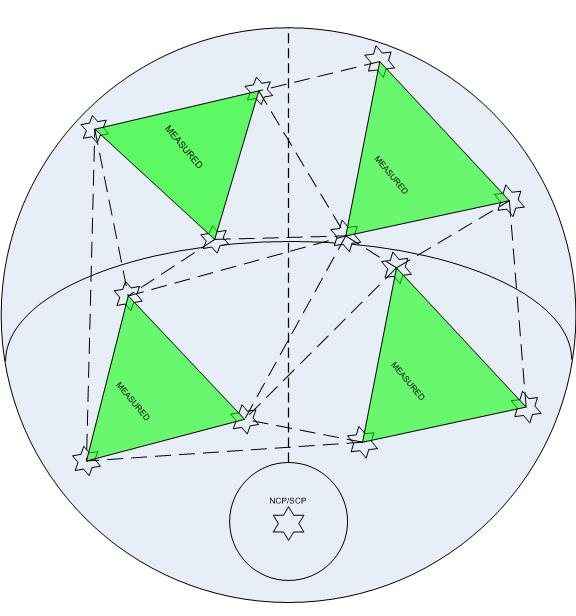
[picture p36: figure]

Figure 20: Twelve Point Alignment as implemented with 3 Point measured on each four corners of the sky

Page 22 of 28

### N-Point Alignment (3-Point+Nearest Transform)

The N-Point is the ultimate in arcsecond (or sub arcseconds) pointing accuracy as you are already painting the entire sky (Figure 21) with mapping data to your mount's stepper coordinate space. EQASCOM still applies the 3-point model scheme but dynamically chooses the three nearest alignment points form the N-Point List to implement the AFFINE/TAKI transformation.

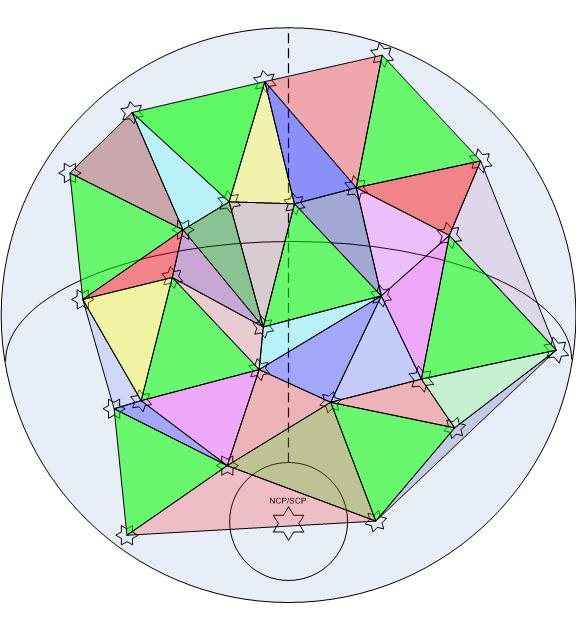
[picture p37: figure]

Figure 21: Multiple Point Alignment as measured on almost the entire sky

Page 23 of 28

### N-Point Alignment (Nearest Point Transform)

You could view this alignment model as being multiple 1-point. You might decide to evenly spread alignment points over the sky or may choose to locate them only nearby objects of interest to act as a local sync point. Whilst using the nearest point transform is potentially not a accurate as a 3-point approach it does have the advantage that if at any point you feel the pointing accuracy is suffering you can simply add a new point local to your intended target confident that pointing will improve (with 3-Point there is no guarantee that the best available alignment triangle obtained using local points)

Page 24 of 28

## Getting most out of the N-Point

EQASCOM's N-Point Model gives the user enough flexibility in mapping out the Sky's coordinate space with your system's coordinate space. However N-Point in itself may be a time-consuming activity for some, especially if they are required to add more alignment stars in the driver's database to drive up the pointing accuracy of the mount. Here are a couple of steps to follow to make the N-Point experience an enjoyable one;

- EQASCOM provides a facility to save the N-Point data and allows the user to re-use the same data even days after the star alignment activity. This means you can always re-use the same database on succeeding sessions.
- To be able to re-use the N-Point data and to maintain its level accuracy, the PC has to by synchronized always to an accurate time referencing system such as a GPS or an internet based atomic clock prior to a N-Point alignment session and before an observing or imaging session.
- Mount has to be parked at the end of any observing session, OTA should not be moved. RA/DEC clutches should be kept tight.
- Any accessory mounted on the OTA can contribute to flexure. If one wishes to maintaining the same level of arcseconds of accuracy, the same accessory configuration should be maintained before and after any alignment (N-Point table population procedure) activity.
- GOTO accuracy should be OK mostly for 3 to 4 alignment stars in "N-Point+Nearest" configuration.
- Accuracy should be OK even with 1 Point or 2 Point provided that the mount is accurately polar aligned and have minimal Cone errors
- You can use EQASCOM's "Append On Synch" mode to populate the N-Point table by simply SYNCING on nearby stars with the Planetarium Program Sync function. Adding more alignment point in its database means MORE 3-Point Triangles are added and would mean a wider triangle area for landing accurate target GOTO objects.
- You can initially start with a 3-Point alignment configuration during your observing session and do a nearby star SYNC (while in Append on Synch mode) as you move from one object to the next object. This way you can "interleave" your observing session with the N-Point alignment session and further increase the pointing accuracy as you go along the way.
- Use the EQASCOM “proximity range” slider to prevent clusters of closely packed alignment points. When adding a new alignment point a search is made of the existing points and any that fall within "range" of the new point are automatically removed from the list. The allowable range is 0-15 degrees in 1 degree steps. So if set to a maximum then any point within a 15 degree movement of either the RA or DEC axis would be removed.
- Use the Points List window to monitor the distribution of points in your model and to see which points are currently being used to apply pointing correction.
- If you mount/telescope exhibits significant flexure or mirror shift then Nearest Star transformation may deliver better performance due to the fact correction is always based upon a local point.

Page 25 of 28

## N-Point Mapper

The N-Point mapper allows users to view the coordinate transformation map of the entire sky based on the current N-Point data.

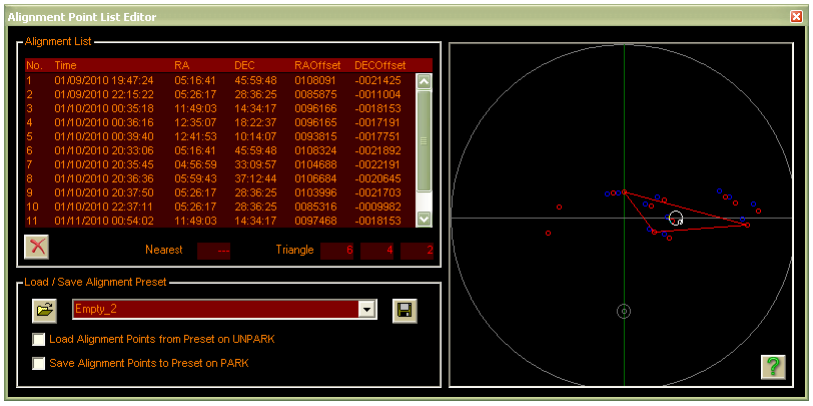
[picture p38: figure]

Using the same N-Point data as shown above, a coordinate transformation map of the entire sky is drawn showing the actual coordinate shift from the Catalog location going to the apparent location (transformed coordinates) as represented by a line with the transformed coordinates portion marked by a grey cross. (See figure below)

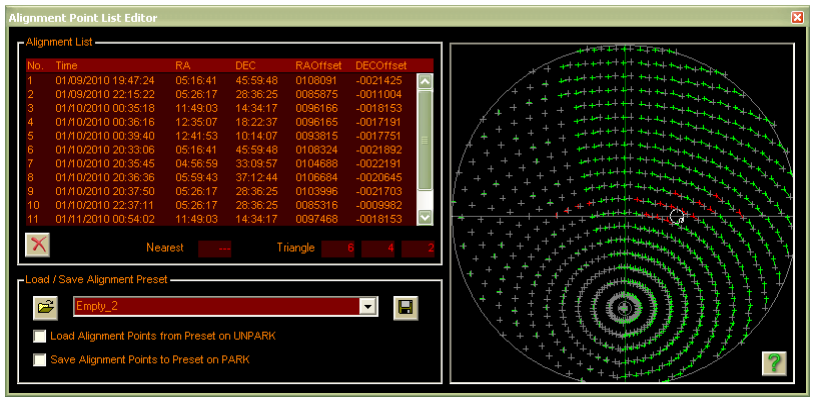
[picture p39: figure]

The transformations marked with a red line are coordinate data that falls within the 3-point triangle. This is where the gotos are most accurate. The ones marked with green lines are those transformed coordinates using the nearest star method.

Page 26 of 28

You can see how the driver dynamically chooses the alignment method across the sky based on the stored N-Point data arrangement.

Page 27 of 28

## FAQs

Q: My Synscan provides 1-Star, 2-Star and 3-Star alignment. What modes does EQASCOM provide? A: EQASCOM provides MultiPoint Alignment. Its up to you how many alignment points you want to use. If you want the equivalent of “1-Star” the you simply clear the alignment data and add a single point to the alignment list.

Q: Can I change between Sync and Dialog based alignment methods once an alignment list has been started?
A: Yes, you can change the alignment method/interface at any time.

Q: Can I switch between “Nearest Point” and “3-Point+Nearest” at any time.
A: Yes.

Q: I use an external program to provide pointing correction. What settings should I apply in EQASCOM?
A: Set the alignment interface method to “Dialog”. Clear any existing alignment and sync data. Ensure that alignment data isn't being automatically loaded on unpark or saved on park (these are options on the Edit Points List screen). EQASCOM will then only provide a sync correction to pointing if it receives ASCOM Syncs command.

Page 28 of 28

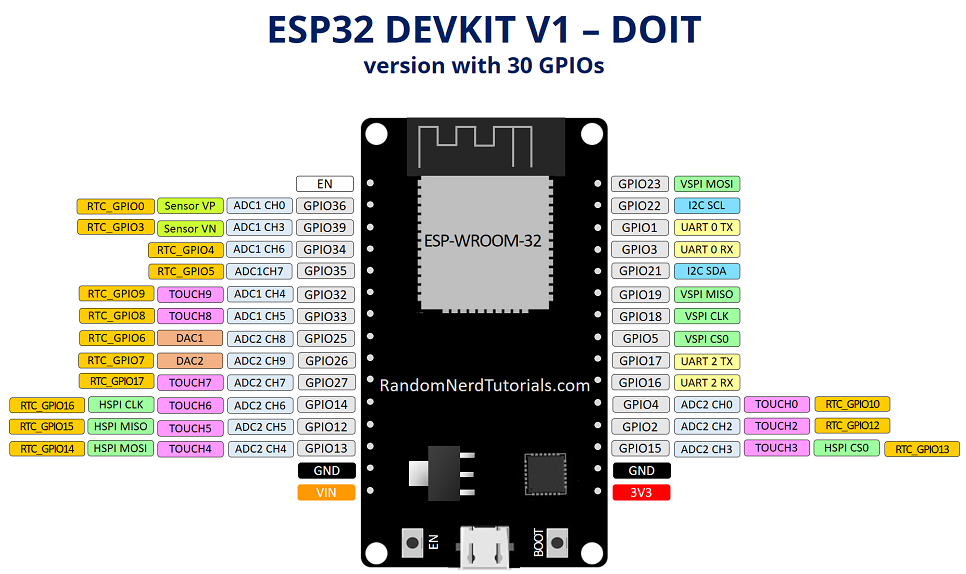
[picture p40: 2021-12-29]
docs/ESP32-DOIT-DEVKIT-V1-Board-Pinout-30-GPIOs.png

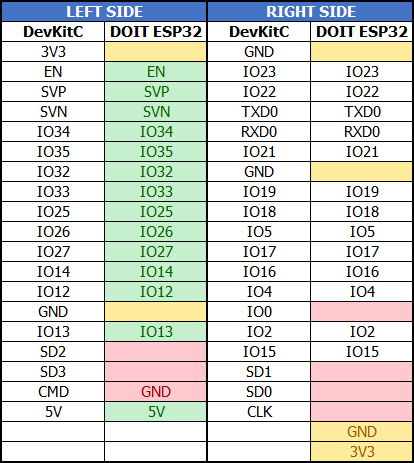
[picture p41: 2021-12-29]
docs/DOIT_ESP32_vs_Espressif_DevKitC_pinout.png

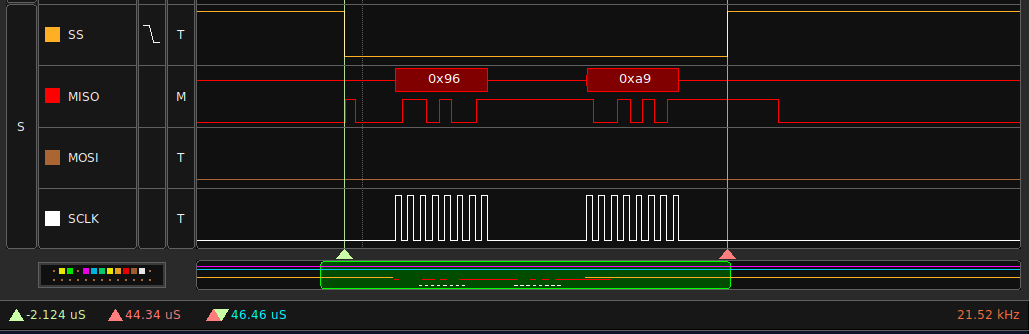
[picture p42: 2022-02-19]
docs/spi-transfer.png

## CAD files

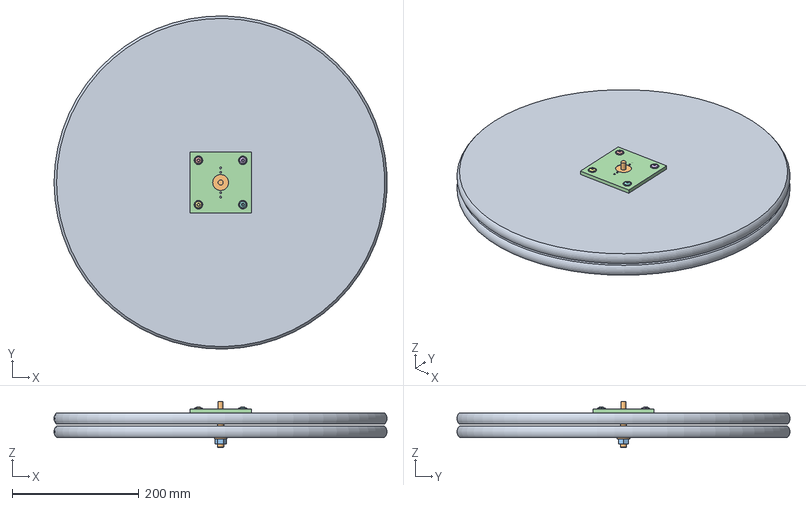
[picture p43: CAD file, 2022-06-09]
cad/assembly.FCStd
525.5 x 525.6 x 73.0 mm
M10-Washer
M10-Nut
M6x16-Screw
M6x16-Screw007
M6x16-Screw008
M6x16-Screw009
Upper Plate

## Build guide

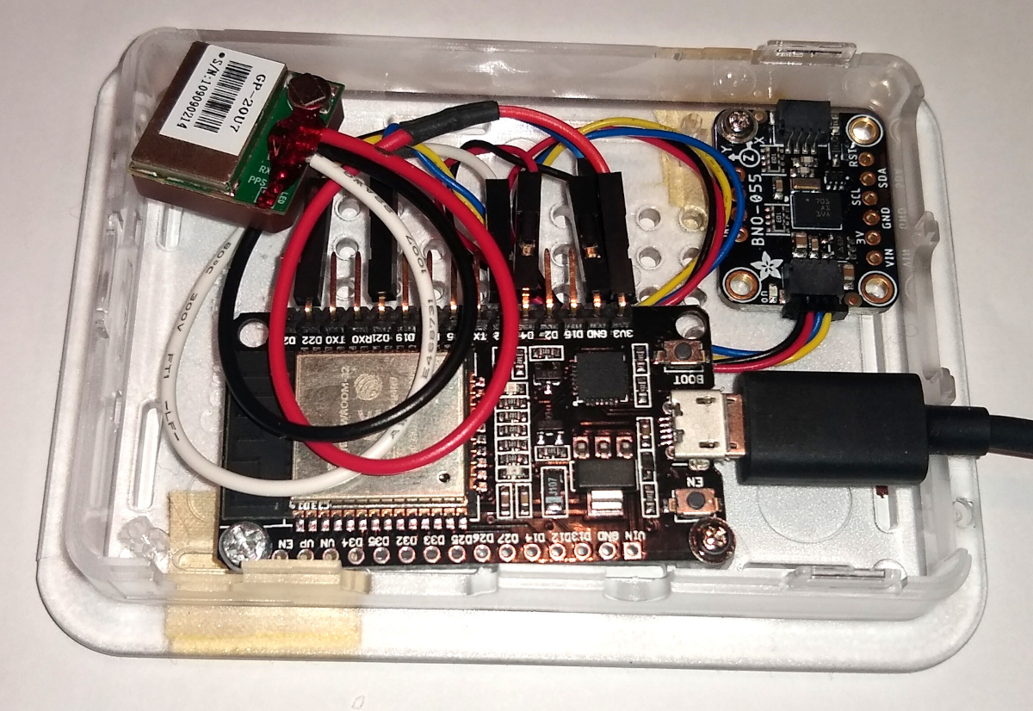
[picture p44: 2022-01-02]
docs/prototype-assembly.jpg

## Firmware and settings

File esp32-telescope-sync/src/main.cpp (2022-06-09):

// own libraries
#include <persistency.h>
#include <telescope.h>
#include <gnss.h>
#include <nexstar.h>
#include <mqttbroker.h>
#include <helper.h>
#include <ledmanager.h>
#include <lsm6wrapper.h>

/**
 * A file called 'secrets.h' must be placed in 'lib/secrets' and contain the following content:
 *
 * #ifndef SECRETS_H
 * #define SECRETS_H
 * struct Secrets
 * {
 *     const char *wifiSsid = "test";   // WiFi AP-Name
 *     const char *wifiPassword = "1234";
 *     IPAddress mqttBroker = IPAddress(192, 168, 1, 1);    // your MQTT-Broker
 *     const char *accessPointSsid = "ESP32";
 *     const char *accessPointPassword = "12345678";    // must be 8+ characters
 *     IPAddress accessPointIP = IPAddress(192, 168, 1, 1);
 * } secrets;
 * #endif
 *
 **/
#include <secrets.h>

// external Libraries
#include <PubSubClient.h>
#include <SPIFFS.h>
// #include <AsyncTCP.h>

// Arduino base
#include <Arduino.h>
#include <WiFi.h>
#include "esp_bt_main.h"
#include "esp_bt_device.h"
#include "BluetoothSerial.h"

constexpr bool DEBUG = false;

// global switches for connected devices
constexpr bool ENABLE_WIFI = true;
constexpr bool WIFIMODE_AUTO = true;
constexpr bool WIFIMODE_FORCE_AP = false; // don't try to connect to a wifi-network and set up an AP immediately

constexpr bool ENABLE_MQTT = true;
constexpr bool ENABLE_GNSS = true;
constexpr bool ENABLE_ORIENTATION = true;
constexpr bool ENABLE_ROTATION = true;
constexpr bool ENABLE_BROKER = true;
constexpr char CONTROL_TOPIC[] = "home/appliance/telescope/control";
constexpr bool ENABLE_BLUETOOTH = true;

// I/O settings
constexpr int IMU_PIN_VCC = 4;
constexpr int IMU_PIN_I2C_SCL = 22;
constexpr int IMU_PIN_I2C_SDA = 21;
constexpr int IMU_I2C_CLOCK = 400000U;
constexpr int IMU_BUS_ID = 0;

// Filter settings
constexpr float HEADING_LOWPASS = 0.3;

TwoWire I2CBus = TwoWire(IMU_BUS_ID); // set up a new Wire-Instance
LSM6Wrapper imu(0, 0x6A, &I2CBus);

constexpr int AMT_SS = 15;
SPIClass AMT22(HSPI);

// stores the availability of certain modules
bool orientationSensorAvailable = false;
bool gnssModuleAvailable = false;
bool filesystemAvailable = false;
bool gnssAvailable = false;
bool mqttAvailable = false;
bool localBrokerAvailable = false;
bool bluetoothAvailable = false;

// internal variables
Adafruit_Sensor *accelerometer, *gyroscope;
sensors_event_t accel, gyro, mag;
float roll = 0, pitch = 0, heading = 180;
float gx = 0, gy = 0, gz = 0;
float qw = 0, qx = 0, qy = 0, qz = 0;
float temperature = 0;
bool wifiClientMode = false;
bool wifiAccessPointMode = false;
float headingOffset = 0;
bool nexStarMode = false;

// Network settings and components
#define TCP_SERVER_PORT (10001)
#define SSID "ESP32"
// AsyncServer server(TCP_SERVER_PORT);

WiFiServer server(TCP_SERVER_PORT);
WiFiClient remoteClient;
WiFiClient wifiClient;
PubSubClient mqttClient(wifiClient); // for connecting to a remote broker
MQTTBroker broker(&Serial);          // set-up own broker, needs a HardwareSerial for logging
BluetoothSerial bluetooth;

// Library modules
Persistency persistency;            // load and save data in flash memory
GNSS gnss(48, 11);                  // GNSS data provider; set initial position to enable operation before GNSS fix
Telescope telescope;                // Telescope properties and related calculations
NexStar nexstar(&telescope, &gnss); // Communication to Stellarium-App
LEDManager ledmanager;

// Flow control, basic task scheduler
#define FILTER_UPDATE_RATE_HZ 50
#define SCHEDULER_MAIN_LOOP_US (1000000 / FILTER_UPDATE_RATE_HZ) // ms
float sensorUpdateRate = 0;

uint32_t timestamp;
uint32_t counter2s = 0;
uint32_t counter300s = 0;
uint32_t counter1h = 0;
uint32_t initStage = 0;

uint32_t taskFilterTimer = 0;
uint32_t task25msTimer = 0;
uint32_t task100msTimer = 0;
uint32_t task500msTimer = 0;
uint32_t task1sTimer = 0;
uint32_t task2sTimer = 0;
uint32_t task30sTimer = 0;

uint32_t gnssTimeout = 0;

// multi-purpose static bytearray
uint8_t txBuffer[256];
uint8_t rxBuffer[256];

void mqttCallback(char *topic, byte *payload, unsigned int length)
{
    Serial.print("[  MQTT  ] Message arrived: '");
    Serial.print(topic);
    Serial.println("'");

    if (length < 1)
        return;

    std::string topicStr(topic);
    if (topicStr.find(CONTROL_TOPIC) == std::string::npos)
        return;

    switch ((char)payload[0])
    {
    case '1': // reset all alignment data
        Serial.println("[  MQTT  ] Reset alignment data");
        telescope.alignment.clearAll();
        txBuffer[0] = '0';
        mqttClient.publish(CONTROL_TOPIC, txBuffer, 1);
        break;
    default:
        break;
    }

    // for (uint32_t i = 0; i < length; i++)
    // {
    //     Serial.print((char)payload[i]);
    // }
    // Serial.println();
}

void onWifiDisconnect(WiFiEvent_t event, WiFiEventInfo_t info)
{
    Serial.printf("[  WIFI  ] Disconnected from `` (%i). Reconnecting...\n", info.disconnected.reason);
    WiFi.disconnect();
    WiFi.begin(secrets.wifiSsid, secrets.wifiPassword);
}

void onWifiConnected(WiFiEvent_t event, WiFiEventInfo_t info)
{
    Serial.println("[  WIFI  ] WiFi connected!");
}

void onWifiIPAddress(WiFiEvent_t event, WiFiEventInfo_t info)
{
    Serial.printf("[  WIFI  ] IP=%s\n", WiFi.localIP().toString().c_str());
}

void onBluetooth(esp_spp_cb_event_t event, esp_spp_cb_param_t *param)
{
    if (event == ESP_SPP_SRV_OPEN_EVT)
    {
        Serial.printf("[   BT   ] Client connected (%02X:%02X:%02X:%02X:%02X:%02X)\n",
                      param->srv_open.rem_bda[0], param->srv_open.rem_bda[1], param->srv_open.rem_bda[2],
                      param->srv_open.rem_bda[3], param->srv_open.rem_bda[4], param->srv_open.rem_bda[5]);
    }
    else if (event == ESP_SPP_CLOSE_EVT)
    {
        Serial.printf("[   BT   ] Connection closed\n");
    }
}

void onBluetoothData(const uint8_t *buffer, size_t size)
{
    int32_t nexstarResponseLength = nexstar.handleRequest(buffer, size, txBuffer, sizeof(txBuffer));
    if (nexstarResponseLength > 0)
    {
        bluetooth.write(txBuffer, nexstarResponseLength);
        nexStarMode = true;
    }
}

void setup()
{
    // LED output
    pinMode(LED_BUILTIN, OUTPUT);
    ledmanager.setMode(LEDManager::LEDMode::ON);
    ledmanager.update();
    initStage++;

    // Setup serial connection for debugging
    Serial.begin(115200U);
    delay(500);
    Serial.println();
    Serial.println("[  INIT  ] Telescope Sync 1.0");
    initStage++;

    Serial.printf("[  INIT  ] ChipRevision: 0x%02X   CpuFreq: %uMHz   FlashChipSize: %uKiB   HeapSize: %uKiB   MAC: %s   SdkVersion: %s\n",
                  ESP.getChipRevision(), ESP.getCpuFreqMHz(), ESP.getFlashChipSize() / 1024, ESP.getHeapSize() / 1024, WiFi.macAddress().c_str(), ESP.getSdkVersion());
    initStage++;

    if (ENABLE_WIFI)
    {
        if (WIFIMODE_AUTO && !WIFIMODE_FORCE_AP)
        {
            // connect to your local wi-fi network
            Serial.printf("[  INIT  ] Connecting to Wifi '%s'", secrets.wifiSsid);
            WiFi.begin(secrets.wifiSsid, secrets.wifiPassword);

            // check wi-fi is connected to wi-fi network
            int retries = 5;
            while ((WiFi.status() != WL_CONNECTED) && ((retries--) > 0))
            {
                delay(1000);
                Serial.print(".");
            }

            if (WiFi.status() == WL_CONNECTED)
            {
                Serial.printf(" connected! (IP=%s)\n", WiFi.localIP().toString().c_str());
                WiFi.onEvent(onWifiDisconnect, SYSTEM_EVENT_STA_DISCONNECTED);
                WiFi.onEvent(onWifiConnected, SYSTEM_EVENT_STA_CONNECTED);
                WiFi.onEvent(onWifiIPAddress, SYSTEM_EVENT_STA_GOT_IP);
                wifiClientMode = true;
            }
            else
            {
                Serial.println(" failed!");
                WiFi.disconnect();
            }
        }

        if ((WIFIMODE_AUTO && !wifiClientMode) || WIFIMODE_FORCE_AP)
        {
            Serial.printf("[  INIT  ] Setting up Wifi access point '%s'...", SSID);
            if (WiFi.softAP(secrets.accessPointSsid, secrets.accessPointPassword))
            {
                WiFi.softAPConfig(secrets.accessPointIP, secrets.accessPointIP, IPAddress(255, 255, 255, 0));
                Serial.printf(" done (IP=%s)\n", WiFi.softAPIP().toString().c_str());
                wifiAccessPointMode = true;
            }
            else
            {
                Serial.println(" failed!");
            }
        }
        initStage++;
    }

    Serial.print("[  INIT  ] Mounting file system... ");
    if (SPIFFS.begin(true))
    {
        Serial.println("ok");
        Serial.printf("[  INIT  ] Flash total: %u KiB  available: %u KiB\n", SPIFFS.totalBytes() / 1024, (SPIFFS.totalBytes() - SPIFFS.usedBytes()) / 1024);
        filesystemAvailable = true;
    }
    else
    {
        Serial.println("failed");
        Serial.println("[! INIT  ] An Error has occurred while mounting SPIFFS");
    }
    initStage++;

    if (filesystemAvailable)
    {
        Serial.println("[  INIT  ] file list:");
        File root = SPIFFS.open("/");
        File file = root.openNextFile();
        while (file)
        {
            Serial.printf("[  INIT  ]       %s - %u Bytes\n", file.name(), file.size());
            file = root.openNextFile();
        }
        root.close();
        file.close();
        initStage++;
    }

    if (ENABLE_ORIENTATION)
    {
        // Power-On Motion Sensor
        pinMode(IMU_PIN_VCC, OUTPUT);
        digitalWrite(IMU_PIN_VCC, HIGH);
        delay(500); // wait for power up. Takes around 400ms (T_Sup).
        initStage++;

        // Initialize Environment Sensor
        if (I2CBus.begin(IMU_PIN_I2C_SDA, IMU_PIN_I2C_SCL, IMU_I2C_CLOCK))
        {
            initStage++;
            if (imu.begin())
            {
                imu.setCalibration();
                initStage++;
                orientationSensorAvailable = true;
                Serial.println("[  INIT  ] Found LSM6DS33+LIS3MDL Absolute Orientation Sensor Board");
            }
            else
            {
                Serial.println("[! INIT  ] Could not find orientation sensor. Check wiring!");
            }
        }
        else
        {
            Serial.println("[! INIT  ] Could not setup I2C Interface!");
        }
    }

    if (wifiClientMode || wifiAccessPointMode)
    {
        server.begin();
        Serial.printf("[  INIT  ] TCP-Server listening on port %u\n", TCP_SERVER_PORT);
        initStage++;

        if (ENABLE_BROKER)
        {
            broker.init(1883);
            localBrokerAvailable = true;
            Serial.printf("[  INIT  ] MQTT-Broker listening on port %u\n", 1883);
            // broker.subscribe("home/appliance/telescope/control");
        }

        if (ENABLE_MQTT && wifiClientMode)
        {
            Serial.print("[  INIT  ] Connecting to remote MQTT-Broker... ");
            mqttClient.setServer(secrets.mqttBroker, 1883);
            mqttClient.setCallback(mqttCallback);
            Serial.println("ok");
            initStage++;
            mqttAvailable = true;
        }
    }

    if (ENABLE_BLUETOOTH)
    {
        bluetooth.enableSSP();
        if (bluetooth.begin(SSID))
        {
            bluetoothAvailable = true;
            // https://techtutorialsx.com/2018/03/09/esp32-arduino-getting-the-bluetooth-device-address/
            const uint8_t *deviceAddress = esp_bt_dev_get_address();
            Serial.printf("[  INIT  ] Bluetooth enabled (%02X:%02X:%02X:%02X:%02X:%02X)\n",
                          *(deviceAddress + 0), *(deviceAddress + 1),
                          *(deviceAddress + 2), *(deviceAddress + 3),
                          *(deviceAddress + 4), *(deviceAddress + 5));
            bluetooth.register_callback(onBluetooth);
            bluetooth.onData(onBluetoothData);  // https://github.com/espressif/arduino-esp32/issues/5473
        }
        else
        {
            Serial.println("[! INIT !] Failed to initialize Bluetooth");
        }
    }

    if (ENABLE_GNSS)
    {
        // The GNSS module streams out it's data every second via the serial interface; no further setup required
        Serial2.begin(9600u);
        Serial.print("[  INIT  ] GNSS-Module enabled\n");
    }

    if (ENABLE_ROTATION)
    {
        AMT22.begin();
        // SPI3.setClockDivider(SPI_CLOCK_DIV128);
        digitalWrite(AMT_SS, HIGH);
        pinMode(AMT_SS, OUTPUT);
    }

    Serial.printf("[  INIT  ] Completed at stage %u\n\n", initStage);
    ledmanager.setMode(LEDManager::LEDMode::READY);
}

void checkForConnections()
{
    if (server.hasClient())
    {
        // If we are already connected to another computer,
        // then reject the new connection. Otherwise accept
        // the connection.
        if (remoteClient && remoteClient.connected())
        {
            uint32_t ip = server.available().remoteIP();
            Serial.printf("[ SOCKET ] Already connected. New connection from %u.%u.%u.%u rejected.\n", ip & 0xFF, (ip >> 8) & 0xFF, (ip >> 16) & 0xFF, (ip >> 24) & 0xFF);
            server.available().stop();
        }
        else
        {
            remoteClient = server.available();
            uint32_t ip = remoteClient.remoteIP();
            Serial.printf("[ SOCKET ] Connection accepted from %u.%u.%u.%u\n", ip & 0xFF, (ip >> 8) & 0xFF, (ip >> 16) & 0xFF, (ip >> 24) & 0xFF);
        }
    }
}

void reconnectMQTTClient()
{
    Serial.print("[  MQTT  ] Attempting MQTT connection... ");
    if (mqttClient.connect(WiFi.getHostname()))
    {
        Serial.println("connected");
        mqttClient.subscribe(CONTROL_TOPIC);
    }
    else
    {
        Serial.printf("failed! (0x%02X)\n", mqttClient.state());
    }
}

void loop()
{
    timestamp = micros();

    if ((timestamp - taskFilterTimer) > SCHEDULER_MAIN_LOOP_US)
    {
        sensorUpdateRate = 1000000. / float(timestamp - taskFilterTimer);
        taskFilterTimer = timestamp;

        if (orientationSensorAvailable)
        {
            imu.accSample();
        }
        return;
    }

    // 25ms Tasks
    if ((timestamp - task25msTimer) > 25000L)
    {
        task25msTimer = timestamp;

        ledmanager.update(timestamp);
        return;
    }

    // 100ms Tasks
    if ((timestamp - task100msTimer) > 100000L)
    {
        task100msTimer = timestamp;

        // read filtered accelerometer data and compute pitch from calibrated values
        imu.getMeanAcc(&accel);
        imu.calibrate(&accel, &gyro);
        pitch = atan2(accel.acceleration.x, accel.acceleration.y) * 180 / PI;

        // read rotation sensor data via SPI and verify checksum
        digitalWrite(AMT_SS, LOW);
        uint16_t heading_raw = (AMT22.transfer(0) << 8) | AMT22.transfer(0);
        digitalWrite(AMT_SS, HIGH);
        if (Checksum::verifyAmtCheckbits(heading_raw))
        {
            // update heading if checksum is ok
            // apply simple IIR-Filter
            heading += HEADING_LOWPASS * ((float(heading_raw & 0x3fff) * 360. / 16385.) - heading);
        }

        // update telescope properties with current measurements
        telescope.setOrientation(heading + headingOffset, pitch);

        if (remoteClient && remoteClient.connected())
        {
            uint32_t received = remoteClient.read(rxBuffer, sizeof(rxBuffer));

            if (received > 0)
            {
                int32_t nexstarResponseLength = nexstar.handleRequest(rxBuffer, sizeof(rxBuffer), txBuffer, sizeof(txBuffer));

                if (nexstarResponseLength > 0)
                {
                    remoteClient.write(txBuffer, nexstarResponseLength);
                    nexStarMode = true;
                }
                else
                {
                    Equatorial reference;

                    // check if the packet could be decoded correctly before using it to calibrate the offset
                    if (telescope.unpackPosition(&reference, NULL, rxBuffer, received))
                    {
                        double localSiderealTimeDegrees = MathHelper::getLocalSiderealTimeDegrees(gnss.utcTimestamp, gnss.longitude);
                        Serial.printf("[ SENSOR ] Received Calibration Data  Ra: %.3f Dec: %.3f\n", reference.ra, reference.dec);
                        telescope.addReferencePoint(reference, gnss.latitude, localSiderealTimeDegrees);
                    }
                }
            }
        }

        if (mqttAvailable)
        {
            mqttClient.loop();
        }

        if (!gnss.valid)
        {
            ledmanager.setMode(LEDManager::LEDMode::BLINK_1HZ);
        }
        else if (remoteClient && remoteClient.connected())
        {
            ledmanager.setMode(LEDManager::LEDMode::FLASH_2X_EVERY_5S);
        }
        else
        {
            ledmanager.setMode(LEDManager::LEDMode::FLASH_1X_EVERY_5S);
        }

        // base tasks
        if (wifiClientMode || wifiAccessPointMode)
            checkForConnections();

        if (localBrokerAvailable)
            broker.update();

        if (DEBUG)
        {
            // send data for SerialStudio
            Serial.printf("/*%f,%f,%f,%f,%f,%f,%f,%f,%f,%f,%f,%f,%f,%f,%f,%f,%f*/\n",
                          heading, pitch, roll,
                          qw, qx, qy, qz,
                          accel.acceleration.x, accel.acceleration.y, accel.acceleration.z,
                          gyro.gyro.x, gyro.gyro.y, gyro.gyro.z,
                          mag.magnetic.x, mag.magnetic.y, mag.magnetic.z,
                          sensorUpdateRate);
        }
        return;
    }

    // 500ms Tasks
    if ((timestamp - task500msTimer) > 500000L)
    {
        task500msTimer = timestamp;

        if (ENABLE_GNSS)
        {
            int received = Serial2.read(rxBuffer, sizeof(rxBuffer) - 1);
            if (received > 0)
            {
                rxBuffer[received] = 0;
                if (gnss.fromBuffer(rxBuffer, received) > 0)
                {
                    // reset timeout counter if we received a valid NMEA sentence
                    gnssTimeout = 4 * 5; // 5s
                    gnssAvailable = true;
                }
                // Serial.printf("[  GNSS  ] %s\n", rxBuffer);
            }
            else
            {
                // check if there is no data from the gnss-unit for a while and set state accordingly
                gnssTimeout -= (gnssTimeout > 0) ? 1 : 0;
                gnssAvailable = gnssTimeout > 0;
            }
        }

        if (orientationSensorAvailable)
        {
            double localSiderealTimeDegrees = MathHelper::getLocalSiderealTimeDegrees(gnss.utcTimestamp, gnss.longitude);
            TransformationType transformationType;
            Equatorial position = telescope.getCalibratedOrientation(gnss.latitude, localSiderealTimeDegrees, transformationType);
            Horizontal corrected = telescope.equatorialToHorizontal(position, gnss.latitude, localSiderealTimeDegrees);

            if (remoteClient && remoteClient.connected() && gnssAvailable && !nexStarMode)
            {
                uint64_t timestamp = 0;
                uint32_t length = telescope.packPosition(position, timestamp, txBuffer, sizeof(txBuffer));
                if (length == 24)
                {
                    remoteClient.write(txBuffer, length);
                }
            }

            int32_t len = 0;
            len = snprintf((char *)txBuffer, sizeof(txBuffer), "%.3f", corrected.alt);
            if (mqttAvailable)
                mqttClient.publish("home/appliance/telescope/alt", txBuffer, len);
            if (localBrokerAvailable)
                broker.publish("home/appliance/telescope/alt", (char *)txBuffer);

            len = snprintf((char *)txBuffer, sizeof(txBuffer), "%.3f", corrected.az);
            if (mqttAvailable)
                mqttClient.publish("home/appliance/telescope/az", txBuffer, len);
            if (localBrokerAvailable)
                broker.publish("home/appliance/telescope/az", (char *)txBuffer);

            len = snprintf((char *)txBuffer, sizeof(txBuffer), "%.3f", position.ra);
            if (mqttAvailable)
                mqttClient.publish("home/appliance/telescope/ra", txBuffer, len);
            if (localBrokerAvailable)
                broker.publish("home/appliance/telescope/ra", (char *)txBuffer);

            len = snprintf((char *)txBuffer, sizeof(txBuffer), "%.3f", position.dec);
            if (mqttAvailable)
                mqttClient.publish("home/appliance/telescope/dec", txBuffer, len);
            if (localBrokerAvailable)
                broker.publish("home/appliance/telescope/dec", (char *)txBuffer);

            len = snprintf((char *)txBuffer, sizeof(txBuffer), "%.3f", localSiderealTimeDegrees / 15.);
            if (mqttAvailable)
                mqttClient.publish("home/appliance/telescope/lst", txBuffer, len);
            if (localBrokerAvailable)
                broker.publish("home/appliance/telescope/lst", (char *)txBuffer);

            len = snprintf((char *)txBuffer, sizeof(txBuffer), "%.3f", pitch);
            if (mqttAvailable)
                mqttClient.publish("home/appliance/telescope/pitch", txBuffer, len);
            if (localBrokerAvailable)
                broker.publish("home/appliance/telescope/pitch", (char *)txBuffer);

            len = snprintf((char *)txBuffer, sizeof(txBuffer), "%.3f", heading);
            if (mqttAvailable)
                mqttClient.publish("home/appliance/telescope/heading", txBuffer, len);
            if (localBrokerAvailable)
                broker.publish("home/appliance/telescope/heading", (char *)txBuffer);
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

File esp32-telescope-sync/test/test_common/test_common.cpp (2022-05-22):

#include <unity.h>
#include <telescope.h>
#include <gnss.h>
#include <nexstar.h>
#include <helper.h>

#include "test_mathhelper.hpp"
#include "test_gnss.hpp"
#include "test_nexstar.hpp"
#include "test_telescope.hpp"
#include "test_alignment.hpp"
#include "test_types.hpp"


void process(void)
{
    Test_Types::process();
    Test_Mathhelper::process();
    Test_Alignment::process();
    Test_GNSS::process();
    Test_Telescope::process();
    Test_Nexstar::process();
}

#ifdef ARDUINO
#include <Arduino.h>

void setup()
{
    // NOTE!!! Wait for >2 secs
    // if board doesn't support software reset via Serial.DTR/RTS
    delay(2000);
    pinMode(LED_BUILTIN, OUTPUT);
    Serial.begin(115200);
    Serial.printf("Heap: %u KiB free\n", ESP.getFreeHeap() / 1024);
    process();
}

void loop()
{
    digitalWrite(LED_BUILTIN, HIGH);
    delay(250);
    digitalWrite(LED_BUILTIN, LOW);
    delay(250);
}

#else

int main(int argc, char **argv)
{
    auto start = std::chrono::high_resolution_clock::now();
    process();
    auto stop = std::chrono::high_resolution_clock::now();
    auto duration = std::chrono::duration_cast<std::chrono::microseconds>(stop - start);
    printf("Elapsed time: %lums\n", duration.count() / 1000);
    return 0;
}
#endif

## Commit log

2021-12-12 more sensor research
2021-12-24 Set up ESP32 and Orientation Sensor
    [ESP32-Devkit-v1-30pin.fzz]
2021-12-25 enable basic socket communication
2021-12-25 initial sensor setup
2021-12-28 optimize sensor stuff add calibration routine
2021-12-28 fix cross-platform constant issues
    [main.cpp, test_common.cpp]
2021-12-29 add GNSS stuff
    [ESP32-Devkit-v1-30pin.fzz]
2021-12-30 integrate everything for E2E function add math helper switch to own f_mod
2022-01-02 switch to IMUPLUS mode
    [ESP32-Devkit-v1-30pin.fzz]
2022-01-09 add broker as submodule
    [main.cpp, test_common.cpp, test_embedded.cpp]
2022-01-09 add raw data and temperature
2022-01-11 NexStar prototype implementation
2022-01-12 add nexstar protocol to esp32
2022-01-16 add mqtt-broker and led-manager
    [main.cpp]
2022-01-18 fix calibration issue with integer overflow fix embedded tests
    [main.cpp, test_common.cpp, test_embedded.cpp]
2022-01-22 BNO055 analysis
    [data1.csv, data2.csv, data3.csv]
2022-01-23 add offline sensor calibration notebook
2022-01-23 prepare calibration
2022-01-23 More offline calibration
2022-01-24 more sensor calibration
2022-01-27 new class for ST sensors
2022-01-28 migrate application to new sensor
2022-01-29 new calibration sketch I2C Noise Comparison
    [main.cpp]
2022-02-02 Gyro Autocalibration
2022-02-19 switch to AMT22-Sensor
    [ESP32-Devkit-v1-30pin.fzz]
2022-02-19 clean-up, switch to DSOX
2022-02-20 filter design for accelerometer accelerometer calibration remove AHRS library
    [plate.FCStd]
2022-03-05 refactor some math code
    [plate.FCStd]
2022-03-06 add test-coverage report clean-up telescope class more unit-tests
    [plate.FCStd]
2022-03-08 fix code coverage fix tranformation matrix bug improve unit-tests
    [main.cpp]
2022-03-29 add more unit-test clean up code
    [plate.FCStd]
2022-04-07 add clear Alignment provide transformationType fix negative dec for nexstar more tests
    [main.cpp]
2022-04-20 fix bluetooth rx buffer issue and clean up
    [main.cpp]
2022-05-02 add bracket
    [plate.FCStd]
2022-05-09 new drawing
    [assembly.FCStd, plate.FCStd]
2022-05-17 switch to Horizontal coordinate system to fix alignment drift bug
    [main.cpp, test_common.cpp]
2022-05-18 switch to point-type based alignment
2022-05-22 add temperature sensor readout more unit-tests and improved test-script
2022-06-06 add assembly drawing describe alignment add references
2022-06-09 add IIR-filter for heading describe mechanical setup and sensor noise
    [assembly.FCStd, plate.FCStd]
